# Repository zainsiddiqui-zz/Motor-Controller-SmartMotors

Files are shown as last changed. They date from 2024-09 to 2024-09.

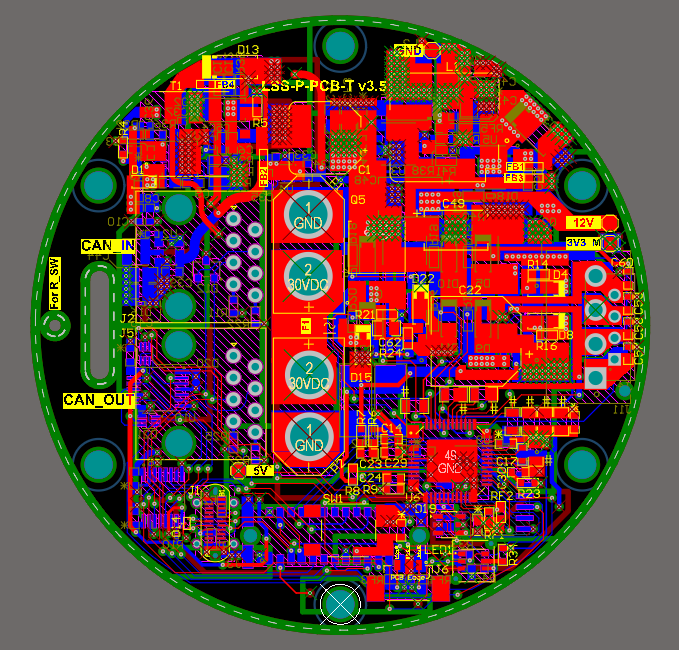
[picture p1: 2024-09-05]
Design-Files/LSS_Top_Board_v3.5/Renderings/2D_C_View.PNG

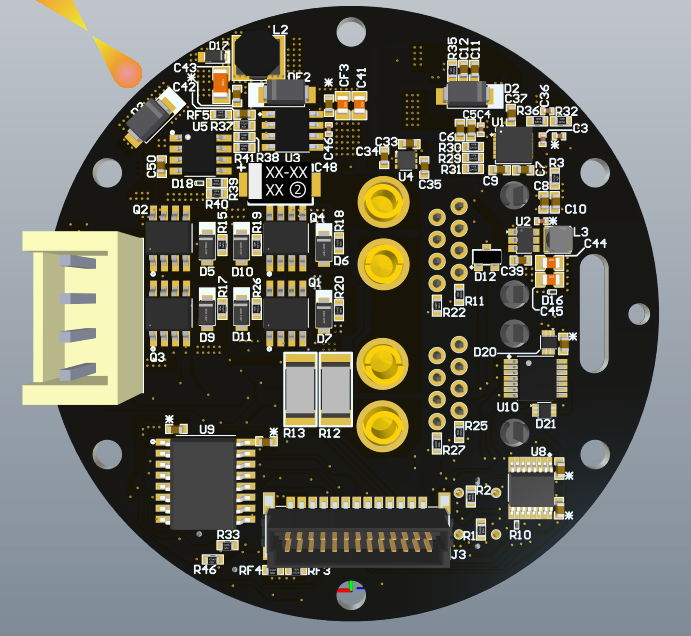
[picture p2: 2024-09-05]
Design-Files/LSS_Top_Board_v3.5/Renderings/3D_Bottom_View.PNG

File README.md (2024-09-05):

# ColeBenson-SmartMotors
 To create a smart motor system involving CAN Interface using STM32 MCU

## Firmware Upload document
https://docs.google.com/document/d/19JVTQ4CaA7uRBn9ySZQGZ3367nQTQ1OMFeYGk8ieIa8/edit#heading=h.wwlx76fb44li

## Branch Information
### main Branch
This branch contains the design submitted to client and is fabricated for testing. Firmware team should use this design for referencing with the board.

### Evaluation Branch
This branch contains the changes currently in progress. After the design is produced and fabricated, this branch will also contain corrections applied that are observed during testing of the hardware.

### Hardware-Prototype-v.3.2 Branch
This branch is referenced from Evaluation-TLE5012B branch. It will contain the final revisions / corrections needed in the hardware.

### Evaluation-TLE5012B Branch
This branch contains the changes currently in progress. After the design is produced and fabricated, this branch will also contain corrections applied that are observed during testing of the hardware. This is an extended branch of Evaluation that has TLE5012B as the magnetic encoder instead of AEAT-8800 chip.

### Hardware-Prototype-v.1 Branch
This branch contains design files for the last set of prototypes that failed to work due to noise issues.

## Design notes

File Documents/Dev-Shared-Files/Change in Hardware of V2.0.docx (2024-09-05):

# TABLE OF CONTENTS

# TABLE OF FIGURES

# HARDWARE DESIGN CHANGES

## ERROR IN 12V REGULATOR OUTPUT VOLTAGE

### PROBLEM

The first issue observed in the design was with the output of DC DC Regulator U3 which was observed to be around 30V when powered up whereas it was expected to be 12V as per calculations. After investigation, it was discovered that the FB pin was appearing as shorted to GND thus causing same voltage as the input to appear at the output. The root cause of this was discovered to be a fabrication error where resistors R38 and R41 were swapped during assembly process as can be observed in Figure

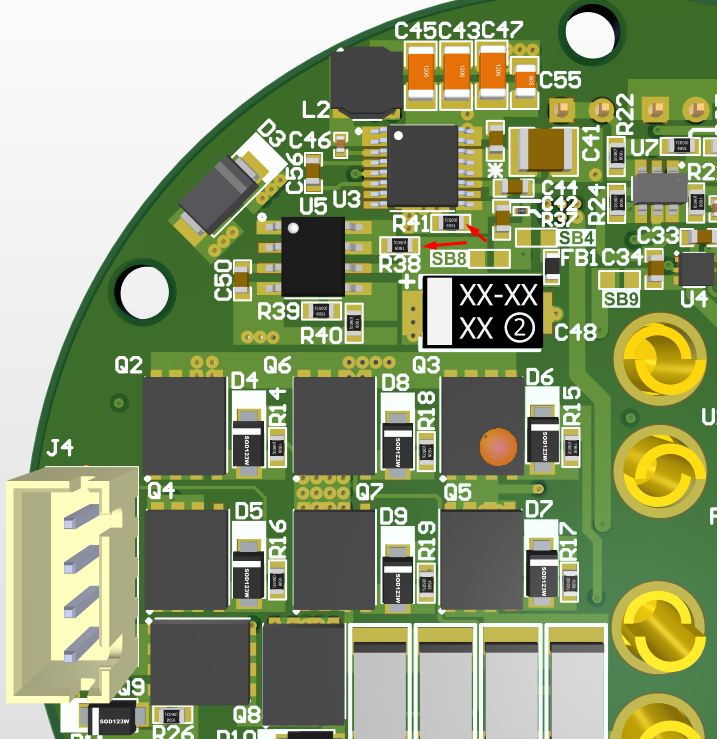
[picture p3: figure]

Figure 1 Image showing R41 and R38 swapped with each other

### SOLUTION

After swapping R38 and R41 to their actual values, the output from U3 was then observed to be correct, measured at 12.4V.

## INCORRECT OUTPUT FROM FLYBACK TRANSFORMER

### PROBLEM 01

The symbol and pin of Transformer component 750314597 was found to be incorrect causing connections to be incorrect in the schematic.

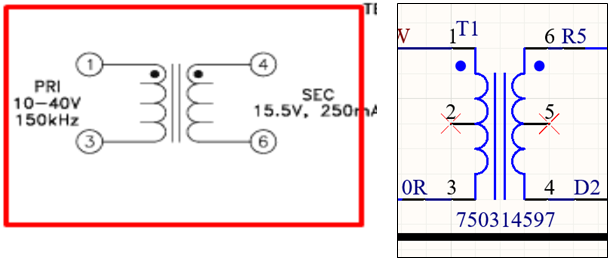
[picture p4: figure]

Figure 2 Image showing correct symbol (left) and incorrect symbol (right). Observe pin 4 and pin 6 of transformer

### SOLUTION

The other end of Resistor R5 (0 ohms) connected to ISO_GND was pulled out and connected to 3V8. Similarly, the other end of Diode D2 connected to 3V8 was pulled out and manually connected to ISO_GND.

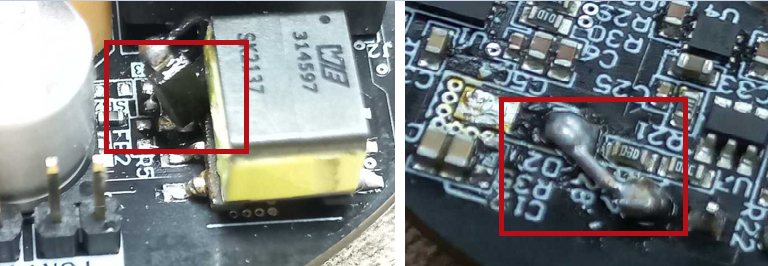
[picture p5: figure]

Figure 3 Diode placed manually on pin 6 (left) and pin 4 of transformer directly short with ISO_GND (right)

### PROBLEM 02

The next problem with this circuit was the feedback resistors were calculated incorrectly causing 8.66V to appear at the output instead of required 3.8V.

### SOLUTION

To obtain the required voltage at the output of the transformer, we need to include forward voltage drop of the secondary rectifier diode as mentioned in the datasheet. The voltage at the input of the transformer, if transformer with turns ratio of 1:1.5 (N1:N2) is selected, is calculated to be 3.0V according to the Equation 22 Pg. 24 of the LM5160ADNTR datasheet.

Figure 4 Formula for calculating Vout at the secondary of transformer

Following changes were made in hardware to achieve the desired output.

1. Change R31 to 100KΩ to set Fsw to 300 KHz, as we have set the output voltage to 3.0V at the primary side of the transformer. LM5160ADNTR Datasheet Pg#19 Equation 12.

Figure 5 Formula for setting switching frequency of transformer to 300 KHz

2. Change R4 to 7.8KΩ for the feedback network to achieve 3.0V at the output on the primary side of the fly-back transformer. The transformer will then step up the voltage and provide the isolated 3.8V at the output.

Figure 6 Formula for calculating output at the secondary of transformer 3.8V

## INCORRECT MAPPING OF SIGNAL AT INTERCONNECT

### PROBLEM

The previous phase of prototypes saw the connections to be accurate but only the incorrect soldered in reverse manner due to overlay issue from designer. This was fixed in this version of prototypes but the connections weren’t mapped according to the new changes in symbol hence causing mismatching between the signals as can be observed in Figure 7.

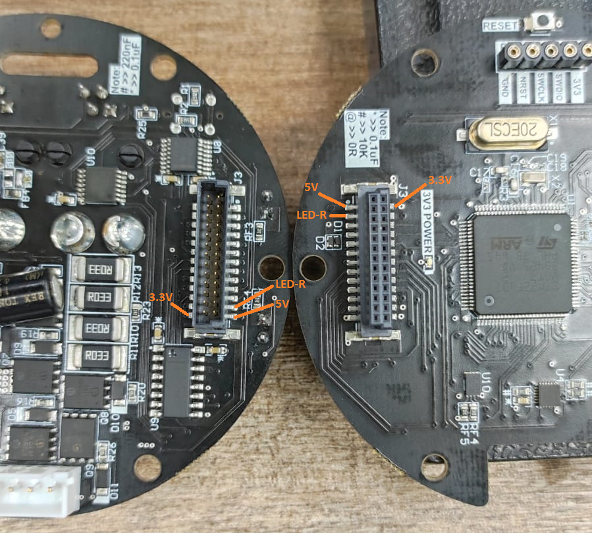
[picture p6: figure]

Figure 7 Error in mapping of interconnect signals

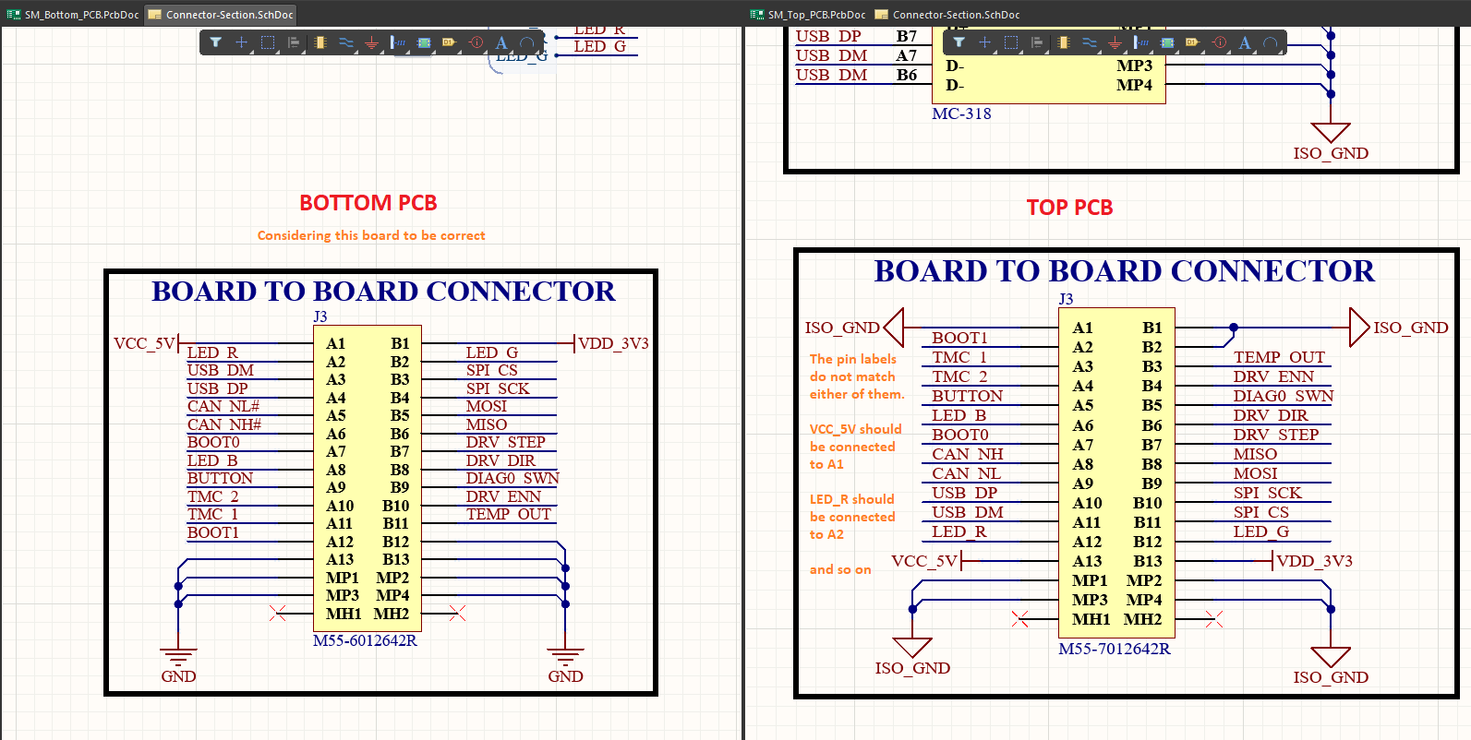
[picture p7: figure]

Figure 8 Image showing connection error with bottom PCB taken as correct reference

### SOLUTION

For the testing, the actual interconnects were removed from the board and a custom ribbon cable was manually soldered in the place to allow for further testing and proper connectivity between Top and Bottom Board

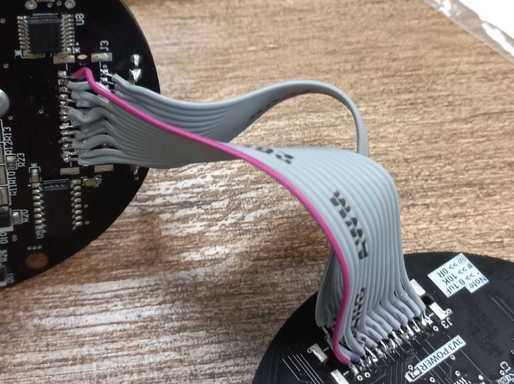
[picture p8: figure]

Figure 9 Image shows manual ribbon cable connections between Top and Bottom Board

## LED RESISTANCE MISSING

### PROBLEM

In the RGB LED LTST-G683GEBW on Top board, the current limiting resistor on the RED LED is missing.

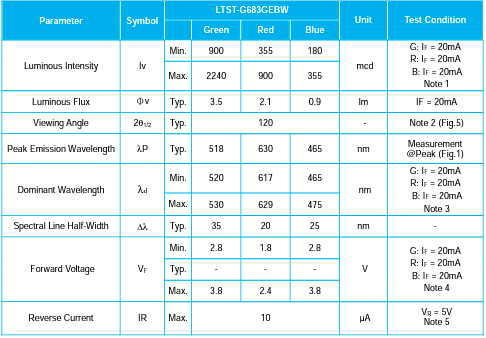
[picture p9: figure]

Figure 10 Image showing values for calculating LED series resistance

### SOLUTION

Add a resistor of 560Ω to it. Only the RED LED is troublesome. The other LEDs are working fine and properly.

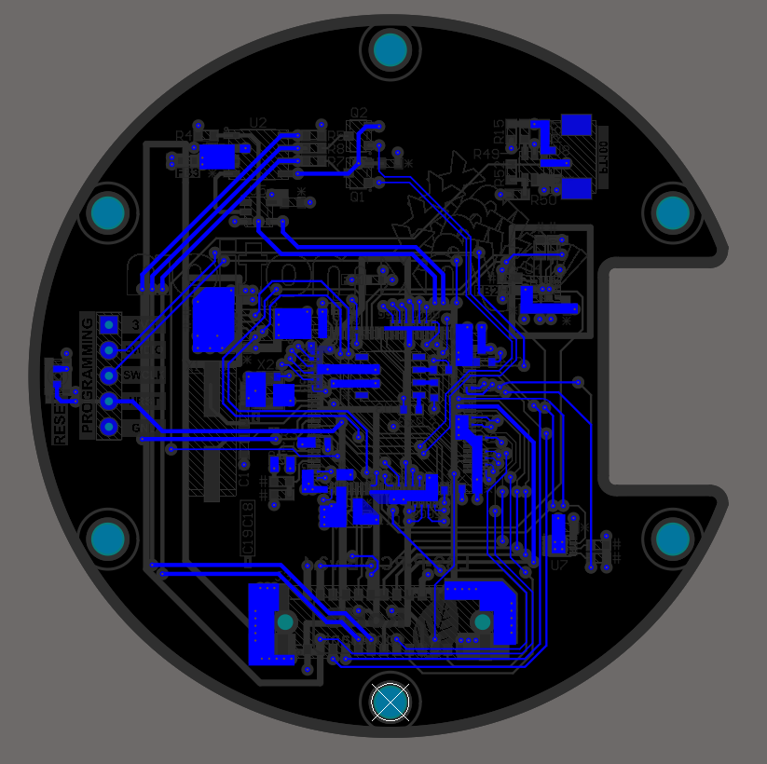
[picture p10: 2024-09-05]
Design-Files/LSS_Bottom_Board_v3.4/Renderings/2D_Bottom_View.PNG

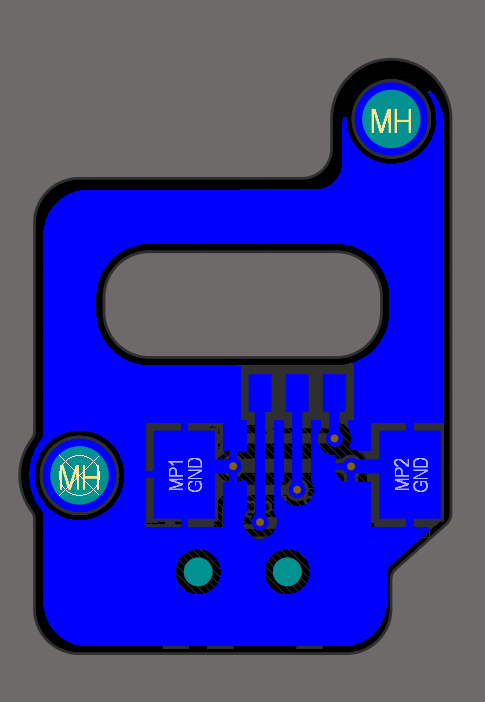
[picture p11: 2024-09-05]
Design-Files/LSS_Sub_Board_v1.1/Renderings/2D_Bottom_View.PNG.png

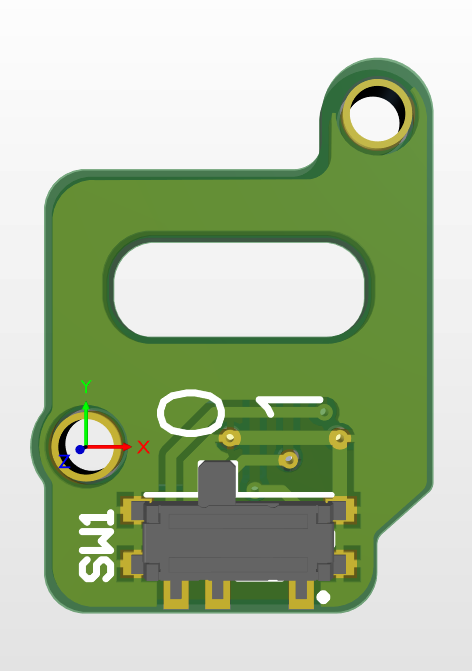
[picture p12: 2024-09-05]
Design-Files/LSS_Sub_Board_v1.1/Renderings/3D_Top_View.PNG.png

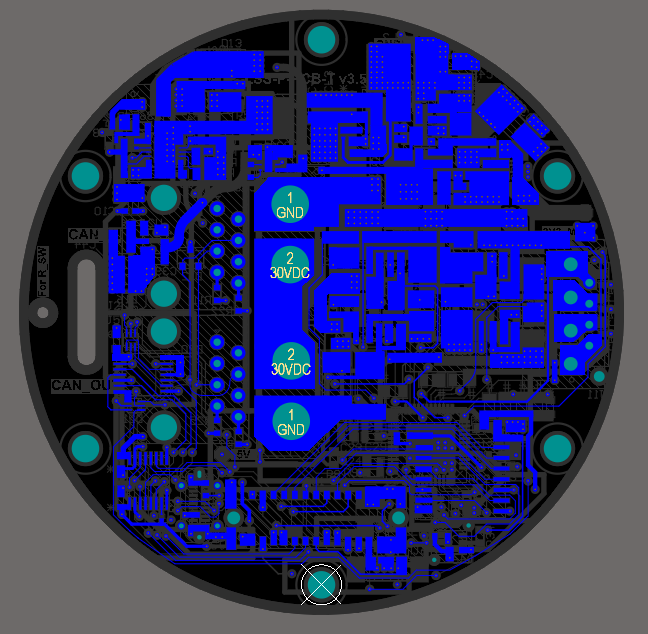
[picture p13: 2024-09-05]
Design-Files/LSS_Top_Board_v3.5/Renderings/2D_Bottom_Layer.PNG

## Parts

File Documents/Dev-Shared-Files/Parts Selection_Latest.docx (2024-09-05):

Parts Selection – Cole Ajode

1. Gyroscope
  a. ITG-3701-Operates on 3.3V (b/w 1.71 to 3.6V) – 12.74$
  b. IAM-20680HP – 16.81$
2. Encoders
  a. AEAT-6600-T16 – 7.78$
  b. AS5215OM-HMFP – 7.56$
  c. AS5134-ZSSM – 6.74$
  d. AS5047D-ATST – 6.83$
3. Motor Drivers
  a. L6207D – 6.85$
  b. DRV8860PWPR – 3.22$
  c. HIP4020IB – 3.47$
4. Voltage Regulators
  a. 24V
- DC-DC Converters
      1. DBS700B24-T – 24V/696W – 312.71000$
  b. 12V
- DC-DC Converters
      1. SIC451ED-T1-GE3 – 25A – 3.91$

Built-in 5V Regulator

      2. EHHD006A0B41Z – 72W – 6A – 30.82$
      3. TSR 1-24120SM – 12W – 1A – 9.2$
      4. UWF1212S-3WR3 – 3W – 250mA – 8.16$
      5. TES 3-2412WI – 3W – 250mA – 33.6$
      6. TIM 2-2412SM – 2W – 167mA – 28.2$
      7. TMR 1-2412SM - 1W – 83mA – 12.42$
- IC’s
      1. MPQ4436AGRE-AEC1-Z – 6A – 3.40$
      2. BDJ2FC0WFP-E2 – 1A – 0.84$
      3. MIC29151-12WU-TR – 1.5A – 4.13$
  c. 5V
    i. NCP3335ADM500R2G – 0.5A – 0.51$
    ii. MCP1826T-ADJE/DC – 1A – 0.71$
    iii. LM1085ISX-ADJ/NOPB – 3A – 2.1$
  d. 3.3V
    i. LT1584CT-3.3#PBF – 7A – 12.27$
    ii. LM1085ISX-ADJ/NOPB - 3A – 2.1$
    iii. NCP186AMX330TAG – 1A – 0.54$
    iv. NCP3335ADM330R2G – 0.5A – 0.51$
  e. 2.5V
    i. LT1584CT#PBF – 7A – 12.27$
    ii. NCP186AMX250TAG - 1A – 0.67$
    iii. NCP3337MN250R2G – 0.5A – 0.51$
  f. 1.8V
    i. NCP186AMX180TAG – 1A – 0.52$
    ii. NCP3337MN180R2G – 0.5A – 0.51$
5. Microcontroller
    i. STM32F407VGT6J – 32BIT – 1MB FLASH – 100LQFP – 10.78$

CAN Supported device

6. RJ-45 Connector
    i. 7499011121A – 6.83$ OR
    ii. E6588-WA0B44-L – 4.37$
7. USB-C Connector
    i. UJC-HP-G-SMT-TR – 1.44$
    ii. KUSBX-SMT-CS2-B30TR – 1.59$
    iii. USB4065-30-A – 3.0$
8. XT30 Connector
    i. FIT0586 – 30A/500VDC – 1.9$ (Pair of Male and Female Connectors)
    ii. XT30U-F – 0.53$ (LCSC) (https://lcsc.com/product-detail/Power-Connectors_Changzhou-Amass-Elec-XT30U-F_C99102.html)
    iii. XT30U-M – 0.47$ (LCSC) (https://lcsc.com/product-detail/Power-Connectors_Changzhou-Amass-Elec-XT30U-M_C99101.html)
    iv. XT30PW-M (https://lcsc.com/product-detail/Power-Connectors_Changzhou-Amass-Elec-XT30PW-M_C431092.html) – 0.65$ (LCSC (https://lcsc.com/product-detail/Power-Connectors_Changzhou-Amass-Elec-XT30PW-M_C431092.html))
9. DB9 Connector
    i. 2301844-2 – Female – PCB Mount – 2.40$
    ii. 182-009-213R431 – Female – PCB Mount – 2.07$

Note: All Part No.’s are from Digi-Key and prices are in USD.

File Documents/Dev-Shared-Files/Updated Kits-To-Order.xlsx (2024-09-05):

S.No | Component Name | Description | Cost | Quantity | Reference Link | Alternate Links | Remarks
1 | STM32F407VG Development Kit | DISCOVERY STM32F407/STM32F417 | $27.07 | 2 | Digikey (https://www.digikey.ca/en/products/detail/stmicroelectronics/STM32F407G-DISC1/5824404) |  | Ordered
2 | TMC5160 Development Board | BREAKOUTBOARD WITH TMC5160 | $31.00 | 2 | Digikey (https://www.digikey.ca/en/products/detail/trinamic-motion-control-gmbh/TMC5160-BOB/8440397) |  | Ordered
3 | Encoder Development Module | ANGLE 4 CLICK | $35.37 | 2 | Digikey (https://www.digikey.ca/en/products/detail/mikroelektronika/MIKROE-3130/9644672) |  | Ordered
4 | CAN Module Breakout | TI SN65HVD231 CAN TRANSCEIVER | $12.95 | 2 | ~~CopperHill~~ (https://copperhilltech.com/can-bus-mini-breakout-board/) | RobotShop (https://www.robotshop.com/en/waveshare-can-board-sn65hvd230.html) | Please check alterante Link
5 | STLink Debugger | STLINK V3 MODULAR IN-CIRCUIT DEB | $47.62 | 1 | Digikey (https://www.digikey.ca/en/products/detail/stmicroelectronics/STLINK-V3SET/9636028) |  | Ordered
6 | Jumper Wires | 40 Pins 30 cm Male To Male | $5.06 | 2 | RobotShop (https://www.robotshop.com/en/40-pins-30-cm-male-to-male-jumper-wire-flat-cable.html) |  | Order Pending
7 | Jumper Wires | 40 Pin Dual Female To Female | $2.00 | 2 | RobotShop (https://www.robotshop.com/en/40-pin-dual-female-splittable-jumper-wire-30cm.html) |  | Order Pending
8 | Jumper Wires | 40 Pin Dual Male To Female | $3.95 | 2 | RobotShop (https://www.robotshop.com/en/velleman-150mm-m-f-40-pin-jumper-wire-splittable.html) |  | Order Pending
9 | BreadBoard | Full Size - Bare Breadboard | $5.95 | 2 | RobotShop (https://www.robotshop.com/en/full-size-bare-breadboard-830-tie-point.html) |  | Order Pending
10 | Testing Hook | Patch Test Hook | $6.90 | 2 | RobotShop (https://www.robotshop.com/en/full-size-bare-breadboard-830-tie-point.html) |  | Order Pending
11 | Testing Clip | Hook Test Clip | $7.90 | 2 | RobotShop (https://www.robotshop.com/en/dfrobot-hook-test-clip-10-pk.html) |  | Order Pending
12 | PCB Holder | PCB Hand Kit | $34.95 | 2 | RobotShop (https://www.robotshop.com/en/sparkfun-third-hand-kit.html) |  | Order Pending

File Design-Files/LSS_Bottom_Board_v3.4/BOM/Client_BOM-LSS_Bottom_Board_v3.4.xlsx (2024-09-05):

# | Item Type | Designator | Description | Footprint | Manufacturer Part Number | Manufacturer | Value | Quantity | Remarks
1 | Capacitor | C1 | CAP CER 4.7UF 25V X5R 0603 | Cap0603 | CL10A475KA8NQNC | Samsung | 4.7UF | 1
2 | Capacitor | C2, C3, C4, C5, C6, C7, C8, C9, C10, C11, C15, C20, C21, C22, C33, C34, C36, C37, C50, CF1 | Cap Ceramic 0.1uF 50VDC X7R 10% SMD 0603 Paper T/R | Cap0603 | CL10B104KB8NNNC | Samsung | 0.1uF | 20 | * Symbol is used for 0.1uF in PCB
3 | Capacitor | C12 | CAP TANT 1UF 10% 16V 1206 | CAP-CASE A | TAJA105K016RNJ | Kyocera AVX | 1UF | 1
4 | Capacitor | C13, C14 | CAP, 2.2µF, 35V, 10%, X5R, 0603 | Cap 0603 | GRM188R6YA225KA12D | Murata | 2.2uF | 2
5 | Capacitor | C16, C17 | CAP 30pF NP0 0603 50 V ±5 % SMD | Cap 0603 | CC0603JRNPO9BN300 | Yageo | 30pF | 2
6 | Capacitor | C18, C19 | CAP CER 10PF 25V C0G 0201 | CAP 0201 | CGA1A2C0G1E100D030BA | TDK | 10pF | 2
7 | Diode | D12 | TVS DIODE 5V 9.8V SOD923 | SOD-923 | ESD9L5.0ST5G | ON Semiconductor | - | 1
8 | Ferrite Bead | FB1, FB2, FB3, FB4 | Ferrite Beads Multi-Layer 120Ohm 25% 100MHz 2A 45mOhm DCR 0603 Automotive T/R | Custom | MPZ1608S121ATDH5 | TDK | - | 4
9 | Connector | J1 | 1x2P 2P 1 1.25mm 2 -40℃~+85℃ Surface Mount SMD,P=1.25mm,Surface Mount，Right Angle Wire To Board / Wire To Wire Connector ROHS | Custom | 1.25-2PWB | DEALON | - | 1
10 | Connector | J3 | CONN RCPT 26POS 0.05 GOLD SMD | Custom | M55-6012642R | Harwin | - | 1
11 | Ferrite Bead | L1 | Ferrite Beads 120Ohm 25% 100MHz 1.2A 0.13Ohm DCR 0603 Automotive T/R | IND 0603 | FBMH1608HL121-TV | Taiyo Yuden | - | 1
12 | Header | P1 | MACHINE PIN SOCKET 5P 2.54MM PIT | Custom | SMC-1-05-1-GT | Adam Equipment | - | 1
13 | Transistor | Q1, Q2 | TRANS NPN 40V 0.6A SMD SOT23-3 | SOT-23 | MMBT2222A-7-F | Diodes | - | 2
14 | Resistor | R1, R6, R9, R10, R11, R12, R13, R14, R17, R18, R19, R20, R21, R22, R23, R24, R25, R26, R28, R29, R30, R31, R32, R33, R34, R35, R36, R37, R38, R39, R40, R41, R42, R43, R44, R45, R46, R47, R48 | RES SMD 0 OHM JUMPER 1/20W 0201 | Res-0201 | RC0201JR-070RL | Yageo | 0R | 39 | @ Symbol is used for 0R in PCB
15 | Resistor | R2, R27, RF1, RF2, RF3, RF4, RF5 | RES SMD 10K Ohm 1% 1/10W 0603 | Res0603 | RC0603FR-0710KL | Yageo | 10K | 7 | # Symbol is used for 10K in PCB
16 | Resistor | R3 | Res Thick Film 0201 806 Ohm 1% 1/20W ±200ppm/°C Molded SMD SMD Paper T/R | Res-0201 | RMCF0201FT806R | Stackpole Electronics | 806R | 1
17 | Resistor | R4, R5 | RES SMD 1K 0.1W 0603 75 V, Thick Film | Res0603 | RC0603JR-071KL | Yageo | 1K | 2
18 | Resistor | R7, R8 | RES SMD 57.6 OHM 1% 1/10W 0603 | Res0603 | RC0603FR-0757R6L | Yageo | 57R6 | 2
19 | Resistor | R15 | RES SMD 3.01K OHM 1% 1/10W 0603 | Res0603 | ERJ-3EKF3011V | Panasonic | 3.01K | 1
20 | Resistor | R16, R53 | RES SMD 10K Ohm 1% 1/10W 0603 | Res0603 | RC0603FR-0710KL | Yageo | DNP | 2 | Do Not Place # Symbol is used for these Resistors in PCB
21 | Resistor | R49 | RES SMD 11K, 1%, 0.1W, 0603 | Res0603 | RC0603FR-0711KL | Yageo | 11K | 1
22 | Resistor | R50 | RES SMD 12.4K OHM 1% 1/10W 0603 | Res0603 | RC0603FR-0712K4L | Yageo | 12.4K | 1
23 | Resistor | R51 | RES SMD 11.8K OHM 1% 1/10W 0603 | Res0603 | AC0603FR-0711K8L | Yageo | 11.8K | 1
24 | Resistor | R52 | RES SMD 105K OHM 1% 1/10W 0603 | Res0603 | RC0603FR-07105KL | Yageo | 105K | 1
25 | Resistor | Rx1, Rx2 | RES SMD 100 OHM 1% 1/10W 0603 | Res0603 | RC0603FR-07100RL | Yageo | 100R | 2
26 | Resistor | Rx3 | RES SMD 470 OHM 50 V, 0603 100 mW, 1%, RC Series | Res0603 | RC0603FR-07470RL | Yageo | 470R | 1
27 | Switch | SW1 | No NO J pin 50mA 3mm 100MΩ 100000 12V 250gf@±30gf 2.6mm -30℃~+85℃ 0.65mm Black Round Button Brick nogging SPST SMD Tactile Switches ROHS | Custom | GT-TC025D-H0065-L1 | G-Switch | - | 1
28 | IC | U1 | IC MCU 32BIT 512KB FLASH 100LQFP | LQFP-100 | STM32F407VET6 | STMicroelectronics | - | 1
29 | IC | U2 | IC TRANSCEIVER HALF 1/1 8SOIC | SOIC-8 | SN65HVDA1040AQDRQ1 | Texas Instruments | - | 1
30 | IC | U3 | SENSOR ANGLE 360DEG SMD | PG-DSO-8 | TLE5012BE1000 | Infineon | - | 1
31 | IC | U4 | IMUACCEL/GYROI2C/SPI14LGA | 14 LGA (2.5x3) | LSM6DSLTR | STMicroelectronics | - | 1
32 | IC | U5 | IC BUF NON-INVERT 5.5V SOT23-5 | SOT-23-5 | SN74LV1T34DBVR | Texas Instruments | - | 1
33 | IC | U6 | IC SENSOR THERMAL 3.0V 8TSSOP | 8-TSSOP | MCP9805-BE/ST | Microchip | - | 1
34 | IC | U7 | IC EEPROM 32KBIT I2C 1MHZ 8UDFN | 8-UDFN-EP (2x3) | CAT24C32HU4I-GT3 | ON Semiconductor | - | 1
35 | IC | U8 | IC OPAMP GP 1.7MHZ RRO SOT23-6 | SOT-23-6 | MAX4236EUT+T | Maxim | - | 1
36 | Crystal | X1 | CRYSTAL 20.0000MHZ 18PF SMD | Custom | HCM4920000000ABJT | CITIZEN | 20MHz | 1
37 | Crystal | X2 | Crystals 32.768KHz 7pF | Custom | ECS-.327-7-34B-C-TR | ECS International | 32.768KHz | 1
38 | Peripheral | PT100 | RTD Temp Sensor | - | - | - | -

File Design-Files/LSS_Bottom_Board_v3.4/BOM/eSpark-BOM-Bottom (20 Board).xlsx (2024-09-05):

 |  | Component list |  | Bill of Materials for Project [SM_Bottom_Board.PrjPcb]
 |  | Source Data From: |  | SM_Bottom_Board
 |  | Project: |  | SM_Bottom_Board
 |  | Variant: |  | None
# | Item Type | Designator | Description | Footprint | Manufacturer Part Number | Manufacturer | Alternate Part Number | LCSC Part Number | Value | Quantity | Quantity (20 Boards) | MOQ (20 Boards) | Links | Unit Cost (20 Boards) | Total Cost (20 Boards) | Review
1 | Capacitor | C1 | CAP CER 4.7UF 25V X5R 0603 | Cap0603 | CL10A475KA8NQNC | Samsung | - | C69335 | 4.7UF | 1 | 20 | 40 | LCSC (https://www.lcsc.com/product-detail/Multilayer-Ceramic-Capacitors-MLCC-SMD-SMT_Samsung-Electro-Mechanics-CL10A475KA8NQNC_C69335.html) | $0.0174 | $0.6960
2 | Capacitor | C2, C3, C4, C5, C6, C7, C8, C9, C10, C11, C15, C33, C34, C36, C37, C50, C22, CF1, C21 | Cap Ceramic 0.1uF 50VDC X7R 10% SMD 0603 Paper T/R | Cap0603 | CL10B104KB8NNNC | Samsung | - | C1591 | 0.1uF | 19 | 380 | 400 | LCSC (https://www.lcsc.com/product-detail/Multilayer-Ceramic-Capacitors-MLCC-SMD-SMT_Samsung-Electro-Mechanics-CL10B104KB8NNNC_C1591.html) | $0.0024 | $0.9600
3 | Capacitor | C12 | CAP TANT 1UF 10% 16V 1206 | Custom | TAJA105K016RNJ | Kyocera AVX | - | C7174 | 1uF | 1 | 20 | 25 | LCSC (https://www.lcsc.com/product-detail/span-style-background-color-ff0-Tantalum-span-Capacitors_Kyocera-AVX-TAJA105K016RNJ_C7174.html) | $0.0526 | $1.3150
4 | Capacitor | C13, C14 | CAP, 2.2µF, 35V, 10%, X5R, 0603 | Cap 0603 | GRM188R6YA225KA12D | Murata | - | C86017 | 2.2uF | 2 | 40 | 50 | LCSC (https://www.lcsc.com/product-detail/Multilayer-Ceramic-Capacitors-MLCC-SMD-SMT_Murata-Electronics-GRM188R6YA225KA12D_C86017.html) | $0.0596 | $2.9800
5 | Capacitor | C16, C17 | CAP 30pF NP0 0603 50 V ±5 % SMD | Cap 0603 | CC0603JRNPO9BN300 | Yageo | - | C113797 | 30pF | 2 | 40 | 100 | LCSC (https://www.lcsc.com/product-detail/Multilayer-Ceramic-Capacitors-MLCC-SMD-SMT_YAGEO-CC0603JRNPO9BN300_C113797.html) | $0.0026 | $0.2600
6 | Capacitor | C18, C19 | CAP CER 10PF 25V C0G 0201 | CAP 0201 | ~~CGA1A2C0G1E100D030BA~~ | TDK | UMK063CG100DTHF | C2168858 | 10pF | 2 | 40 | 50 | LCSC (https://www.lcsc.com/product-detail/Multilayer-Ceramic-Capacitors-MLCC-SMD-SMT_Taiyo-Yuden-UMK063CG100DTHF_C2168858.html) | $0.0064 | $0.3200
7 | Capacitor | C20 | CAP CER 10UF 25V X5R 0603 | Cap-0603 | C1608X5R1E106M080AC | TDK |  | C2168289 | 10uF | 1 | 20 | 21 | LCSC (https://www.lcsc.com/product-detail/Multilayer-Ceramic-Capacitors-MLCC-SMD-SMT_TDK-C1608X5R1E106M080AC_C2168289.html) | $0.4640 | $9.7440
8 | Diode | D12 | TVS DIODE 5V 9.8V SOD923 | SOD-923 | ESD9L5.0ST5G | ON Semiconductor | - | C82326 | - | 1 | 20 | 25 | LCSC (https://www.lcsc.com/product-detail/span-style-background-color-ff0-ESD-span-Protection-Devices_onsemi-ESD9L5-0ST5G_C82326.html) | $0.0617 | $1.5425
9 | Ferrite Bead | FB1, FB2, FB3, FB4 | Ferrite Beads Multi-Layer 120Ohm 25% 100MHz 2A 45mOhm DCR 0603 Automotive T/R | Ferrite0603 | MPZ1608S121ATDH5 | TDK | - | C307770 | - | 4 | 80 | 100 | LCSC (https://www.lcsc.com/product-detail/Ferrite-Beads_TDK-MPZ1608S121ATDH5_C307770.html) | $0.0280 | $2.8000
10 | Connector | J3 | CONN RCPT 26POS 0.05 GOLD SMD | Custom | M55-6012642R | Harwin | - | - | - | 1 | 20 | 22 | Mouser (https://eu.mouser.com/ProductDetail/Harwin/M55-6012642R?qs=rrS6PyfT74ceXT9Rk1eWQA%3D%3D) | $2.5100 | $55.2200
11 | Ferrite Bead | L1 | Ferrite Beads 120Ohm 25% 100MHz 1.2A 0.13Ohm DCR 0603 Automotive T/R | IND 0603 | FBMH1608HL121-TV | Taiyo Yuden | - | C515365 | - | 1 | 20 | 25 | LCSC (https://www.lcsc.com/product-detail/Ferrite-Beads_Taiyo-Yuden-FBMH1608HL121-TV_C515365.html) | $0.0876 | $2.1900
12 | LED | LED1 | LED GREEN CLEAR CHIP SMD | LED 0402 | ~~XZVG68W-2~~ | SunLED | MHT136CGCT | C401111 | - | 1 | 20 | 30 | LCSC (https://www.lcsc.com/product-detail/Light-Emitting-Diodes-span-style-background-color-ff0-LED-span_MEIHUA-MHT136CGCT_C401111.html) | $0.0379 | $1.1370
13 | Header | P1 | MACHINE PIN SOCKET 5P 2.54MM PIT | Custom | SMC-1-05-1-GT | Adam Equipment | - | - | - | 1 | 20 | 25 | Digikey (https://www.digikey.com/en/products/detail/adam-tech/SMC-1-05-1-GT/9831387) | $0.3084 | $7.7100
14 | Test Point | ~~P2, P3, P4, P5, P6, P7~~ | ~~Testing Pad 30 mil Dia~~ | ~~30 mil Test Point~~ | ~~30 mil Test Point~~ | ~~-~~ | ~~-~~ | ~~-~~ | ~~DNP~~ | ~~6~~ | ~~120~~ | ~~-~~ | ~~-~~ | ~~-~~ | ~~-~~ | ~~Do Not Mount~~
15 | Transistor | Q1, Q2 | TRANS NPN 40V 0.6A SMD SOT23-3 | SOT-23 | MMBT2222A-7-F | Diodes | - | C94515 | - | 2 | 40 | 60 | LCSC (https://www.lcsc.com/product-detail/Bipolar-Transistors-BJT_Diodes-Incorporated-MMBT2222A-7-F_C94515.html) | $0.0306 | $1.8360
16 | Resistor | R1, R9, R10, R11, R12, R13, R14, R17, R18, R19, R20, R21, R22, R23, R24, R25, R26, R28, R29, R30, R31, R32, R33, R34, R35, R36, R37, R38, R39, R40, R41, R42, R43, R44, R45, R46, R47, R48 | RES SMD 0 OHM JUMPER 1/20W 0201 | Res-0201 | RC0201JR-070RL | Yageo | - | C106228 | 0R | 38 | 760 | 800 | LCSC (https://www.lcsc.com/product-detail/Chip-Resistor-Surface-Mount_YAGEO-RC0201JR-070RL_C106228.html) | $0.0008 | $0.6400
17 | Resistor | R2, R27, RF1, RF2, RF3, RF4, RF5 | RES SMD 10K Ohm 1% 1/10W 0603 | Res0603 | RC0603FR-0710KL | Yageo | - | C98220 | 10K | 7 | 140 | 200 | LCSC (https://www.lcsc.com/product-detail/Chip-Resistor-Surface-Mount_YAGEO-RC0603FR-0710KL_C98220.html) | $0.0010 | $0.2000
18 | Resistor | R3 | Res Thick Film 0201 806 Ohm 1% 1/20W ±200ppm/°C Molded SMD SMD Paper T/R | Res-0201 | ~~RMCF0201FT806R~~ | Stackpole Electronics | 0201WMF8060TEE | C474262 | 806R | 1 | 20 | 100 | LCSC (https://www.lcsc.com/product-detail/Chip-Resistor-Surface-Mount_UNI-ROYAL-Uniroyal-Elec-0201WMF8060TEE_C474262.html) | $0.0019 | $0.1900
19 | Resistor | R4, R5 | RES SMD 1K 0.1W 0603 75 V, Thick Film | Res0603 | RC0603JR-071KL | Yageo | - | C14676 | 1K | 2 | 40 | 100 | LCSC (https://www.lcsc.com/product-detail/Chip-Resistor-Surface-Mount_YAGEO-RC0603JR-071KL_C14676.html) | $0.0010 | $0.1000
20 | Resistor | R6 | RES SMD 470 OHM 50 V, 0603 100 mW, 1%, | Res0603 | RC0603FR-07470RL | Yageo | - | C114669 | 470R | 1 | 20 | 100 | LCSC (https://www.lcsc.com/product-detail/Chip-Resistor-Surface-Mount_YAGEO-RC0603FR-07470RL_C114669.html) | $0.0013 | $0.1300
21 | Resistor | R7, R8 | RES SMD 57.6 OHM 1% 1/10W 0603 | Res0603 | ~~RC0603FR-0757R6L~~ | Yageo | CR0603-FX-57R6ELF | C203694 | 57R6 | 2 | 40 | 50 | LCSC (https://www.lcsc.com/product-detail/Chip-Resistor-Surface-Mount_BOURNS-CR0603-FX-57R6ELF_C203694.html) | $0.0027 | $0.1350
22 | Resistor | R15, R50, R51, R52 | RES SMD 4.7K OHM 1% 1/10W 0603 | Res-0603 | RC0603FR-074K7L | Yageo | - | C99782 | 4.7K | 4 | 80 | 100 | LCSC (https://www.lcsc.com/product-detail/Chip-Resistor-Surface-Mount_YAGEO-RC0603FR-074K7L_C99782.html) | $0.0012 | $0.1200
23 | Switch | SW1 | No NO J pin 50mA 3mm 100MΩ 100000 12V 250gf@±30gf 2.6mm -30℃~+85℃ 0.65mm Black Round Button Brick nogging SPST SMD Tactile Switches ROHS | Custom | GT-TC025D-H0065-L1 | G-Switch | - | C778132 | - | 1 | 20 | 30 | LCSC (https://www.lcsc.com/product-detail/Tactile-Switches_G-Switch-GT-TC025D-H0065-L1_C778132.html) | $0.0414 | $1.2420
24 | IC | U1 | IC MCU 32BIT 512KB FLASH 100LQFP | 100 LQFP | ~~STM32F407VET6~~ | STMicroelectronics | STM32F407VGT6, STM32F407VET6 | C12345, C28730 | - | 1 | 20 | 22 | LCSC (https://www.lcsc.com/product-detail/Microcontroller-Units-MCUs-MPUs-SOCs_STMicroelectronics-STM32F407VET6_C28730.html) | $10.6528 | $234.3616 | Multiple options added for MCU
25 | IC | U2 | IC TRANSCEIVER HALF 1/1 8SOIC | SOIC-8 | SN65HVDA1040AQDRQ1 | Texas Instruments | - | C188675 | - | 1 | 20 | 22 | LCSC (https://www.lcsc.com/product-detail/CAN-ICs_Texas-Instruments-SN65HVDA1040AQDRQ1_C188675.html) | $1.6387 | $36.0514
26 | IC | U3 | 18B SINGLE MAG ENC MULTIPLE AXIS | 32-QFN (5x5) | AEAT-9955 | Broadcom Limited | - | - | - | 1 | 20 | 21 | Digikey (https://www.digikey.com/en/products/detail/broadcom-limited/AEAT-9955-102/15212630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) | $21.3200 | $447.7200
27 | IC | U4 | IMUACCEL/GYROI2C/SPI14LGA | LGA-14 | ~~LSM6DSLTR~~ | STMicroelectronics | LSM6DSLTR | C126672 | - | 1 | 20 | 22 | LCSC (https://www.lcsc.com/product-detail/Attitude-Sensor-Gyroscope_STMicroelectronics-LSM6DSLTR_C126672.html) | $1.8360 | $40.3920
28 | IC | U5 | IC BUF NON-INVERT 5.5V SOT23-5 | SOT-23-5 | SN74LV1T34DBVR | Texas Instruments | - | C100024 | - | 1 | 20 | 25 | LCSC (https://www.lcsc.com/product-detail/Buffers-Drivers_Texas-Instruments-SN74LV1T34DBVR_C100024.html) | $0.2267 | $5.6675
29 | IC | U6 | IC SENSOR THERMAL 3.0V 8TSSOP | 8-TSSOP | MCP9805-BE/ST | Microchip | - | - | - | 1 | 20 | 22 | Mouser (https://eu.mouser.com/ProductDetail/Microchip-Technology/MCP9805T-BE-ST?qs=QVBMgXxBiLz7mzfqWZNLHA%3D%3D) | $1.0600 | $23.3200
30 | IC | U7 | IC EEPROM 32KBIT I2C 1MHZ 8UDFN | 8-UDFN-EP (2x3) | CAT24C32HU4I-GT3 | ON Semiconductor | - | C233772 | - | 1 | 20 | 22 | LCSC (https://www.lcsc.com/product-detail/EEPROM_onsemi-CAT24C32HU4I-GT3_C233772.html) | $0.5330 | $11.7260
31 | Crystal | X1 | CRYSTAL 20.0000MHZ 18PF SMD | Custom | HCM4920000000ABJT | CITIZEN | - | - | 20MHz | 1 | 20 | 22 | Digikey (https://www.digikey.com/en/products/detail/citizen-finedevice-co-ltd/HCM4920000000ABJT/284290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) | $0.5050 | $11.1100
32 | Crystal | X2 | Crystals 32.768KHz 7pF | Custom | ECS-.327-7-34B-C-TR | ECS International | - | - | 32.768KHz | 1 | 20 | 22 | Mouser (https://eu.mouser.com/ProductDetail/ECS/ECS-.327-7-34B-C-TR?qs=wo4x%252BUeoG8U8yBn%2Foj%2FI7w%3D%3D) | $0.6900 | $15.1800
 |  |  |  |  |  |  |  |  |  |  |  | Total Component Cost |  |  | $917.00
 |  |  |  |  |  |  |  |  |  |  |  | Single Board Cost |  |  | $45.85

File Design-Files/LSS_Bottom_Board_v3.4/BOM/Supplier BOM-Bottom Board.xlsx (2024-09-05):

 |  | Component list |  | Bill of Materials for Project [SM_Bottom_Board.PrjPcb]
 |  | Source Data From: |  | SM_Bottom_Board
 |  | Project: |  | SM_Bottom_Board
 |  | Variant: |  | None
# | Item Type | Designator | Description | Footprint | Manufacturer Part Number | Manufacturer | Value | Quantity | Links | Unit Cost (1 Boards) | Total Cost (1 Boards) | Review
1 | Capacitor | C1 | CAP CER 4.7UF 25V X5R 0603 | Cap0603 | CL10A475KA8NQNC | Samsung | 4.7UF | 1 | LCSC (https://www.lcsc.com/product-detail/Multilayer-Ceramic-Capacitors-MLCC-SMD-SMT_Samsung-Electro-Mechanics-CL10A475KA8NQNC_C69335.html) | $0.0174 | $0.0174
2 | Capacitor | C2, C3, C4, C5, C6, C7, C8, C9, C10, C11, C15, C32, C33, C34, C36, C37, C50, CF1 | Cap Ceramic 0.1uF 50VDC X7R 10% SMD 0603 Paper T/R | Cap0603 | CL10B104KB8NNNC | Samsung | 0.1uF | 18 | LCSC (https://www.lcsc.com/product-detail/Multilayer-Ceramic-Capacitors-MLCC-SMD-SMT_Samsung-Electro-Mechanics-CL10B104KB8NNNC_C1591.html) | $0.0025 | $0.0450
3 | Capacitor | C12 | CAP TANT 1UF 10% 16V 1206 | Custom | TAJA105K016RNJ | Kyocera AVX | 1uF | 1 | LCSC (https://www.lcsc.com/product-detail/span-style-background-color-ff0-Tantalum-span-Capacitors_Kyocera-AVX-TAJA105K016RNJ_C7174.html) | $0.0685 | $0.0685
4 | Capacitor | C13, C14 | CAP, 2.2µF, 35V, 10%, X5R, 0603 | Cap 0603 | GRM188R6YA225KA12D | Murata | 2.2uF | 2 | LCSC (https://www.lcsc.com/product-detail/Multilayer-Ceramic-Capacitors-MLCC-SMD-SMT_Murata-Electronics-GRM188R6YA225KA12D_C86017.html) | $0.0596 | $0.1192
5 | Capacitor | C16, C17 | CAP 30pF NP0 0603 50 V ±5 % SMD | Cap 0603 | CC0603JRNPO9BN300 | Yageo | 30pF | 2 | LCSC (https://www.lcsc.com/product-detail/Multilayer-Ceramic-Capacitors-MLCC-SMD-SMT_YAGEO-CC0603JRNPO9BN300_C113797.html) | $0.0026 | $0.0052
6 | Capacitor | C18, C19 | CAP CER 10PF 25V C0G 0201 | CAP 0201 | UMK063CG100DTHF | TDK | 10pF | 2 | LCSC (https://www.lcsc.com/product-detail/Multilayer-Ceramic-Capacitors-MLCC-SMD-SMT_Taiyo-Yuden-UMK063CG100DTHF_C2168858.html) | $0.0064 | $0.0128
7 | Diode | D1 | TVS DIODE 24VWM 41VC TO236AB | Custom | PESD2CAN,215 | Nexperia | - | 1 | LCSC (https://www.lcsc.com/product-detail/span-style-background-color-ff0-ESD-span-Protection-Devices_Nexperia-PESD2CAN-215_C75176.html) | $0.1772 | $0.1772
8 | Diode | D12 | TVS DIODE 5V 9.8V SOD923 | SOD-923 | ESD9L5.0ST5G | ON Semiconductor | - | 1 | LCSC (https://www.lcsc.com/product-detail/span-style-background-color-ff0-ESD-span-Protection-Devices_onsemi-ESD9L5-0ST5G_C82326.html) | $0.0617 | $0.0617
9 | Ferrite Bead | FB1, FB2, FB3, FB4 | Ferrite Beads Multi-Layer 120Ohm 25% 100MHz 2A 45mOhm DCR 0603 Automotive T/R | Ferrite0603 | MPZ1608S121ATDH5 | TDK | - | 4 | LCSC (https://www.lcsc.com/product-detail/Ferrite-Beads_TDK-MPZ1608S121ATDH5_C307770.html) | $0.0280 | $0.1120
10 | Connector | J3 | CONN RCPT 26POS 0.05 GOLD SMD | Custom | M55-6012642R | Harwin | - | 1 | Mouser (https://eu.mouser.com/ProductDetail/Harwin/M55-6012642R?qs=rrS6PyfT74ceXT9Rk1eWQA%3D%3D) | $2.9300 | $2.9300
11 | Ferrite Bead | L1 | Ferrite Beads 120Ohm 25% 100MHz 1.2A 0.13Ohm DCR 0603 Automotive T/R | IND 0603 | FBMH1608HL121-TV | Taiyo Yuden | - | 1 | LCSC (https://www.lcsc.com/product-detail/Ferrite-Beads_Taiyo-Yuden-FBMH1608HL121-TV_C515365.html) | $0.0876 | $0.0876
12 | LED | LED1 | LED GREEN CLEAR CHIP SMD | LED 0402 | MHT136CGCT | SunLED | - | 1 | LCSC (https://www.lcsc.com/product-detail/Light-Emitting-Diodes-span-style-background-color-ff0-LED-span_MEIHUA-MHT136CGCT_C401111.html) | $0.0399 | $0.0399
13 | Header | P1 | MACHINE PIN SOCKET 5P 2.54MM PIT | Custom | SMC-1-05-1-GT | Adam Equipment | - | 1 | Digikey (https://www.digikey.com/en/products/detail/adam-tech/SMC-1-05-1-GT/9831387) | $0.4100 | $0.4100
14 | Transistor | Q1, Q2 | TRANS NPN 40V 0.6A SMD SOT23-3 | SOT-23 | MMBT2222A-7-F | Diodes | - | 2 | LCSC (https://www.lcsc.com/product-detail/Bipolar-Transistors-BJT_Diodes-Incorporated-MMBT2222A-7-F_C94515.html) | $0.0335 | $0.0670
15 | Resistor | R1, R9, R10, R11, R12, R13, R14, R15, R16, R17, R18, R19, R20, R21, R22, R23, R24, R25, R26, R28, R29, R30, R31, R32, R33, R34, R35, R36, R37, R38, R39, R40, R41, R42, R43, R44, R45, R46, R47, R48 | RES SMD 0 OHM JUMPER 1/20W 0201 | Res-0201 | RC0201JR-070RL | Yageo | 0R | 40 | LCSC (https://www.lcsc.com/product-detail/Chip-Resistor-Surface-Mount_YAGEO-RC0201JR-070RL_C106228.html) | $0.0008 | $0.0320
16 | Resistor | R2, R27, RF1, RF2, RF3, RF4, RF5 | RES SMD 10K Ohm 1% 1/10W 0603 | Res0603 | RC0603FR-0710KL | Yageo | 10K | 7 | LCSC (https://www.lcsc.com/product-detail/Chip-Resistor-Surface-Mount_YAGEO-RC0603FR-0710KL_C98220.html) | $0.0010 | $0.0070
17 | Resistor | R3 | Res Thick Film 0201 806 Ohm 1% 1/20W ±200ppm/°C Molded SMD SMD Paper T/R | Res-0201 | 0201WMF8060TEE | Stackpole Electronics | 806R | 1 | LCSC (https://www.lcsc.com/product-detail/Chip-Resistor-Surface-Mount_UNI-ROYAL-Uniroyal-Elec-0201WMF8060TEE_C474262.html) | $0.0019 | $0.0019
18 | Resistor | R4, R5 | RES SMD 1K 0.1W 0603 75 V, Thick Film | Res0603 | RC0603JR-071KL | Yageo | 1K | 2 | LCSC (https://www.lcsc.com/product-detail/Chip-Resistor-Surface-Mount_YAGEO-RC0603JR-071KL_C14676.html) | $0.0010 | $0.0020
19 | Resistor | R6, Rx3 | RES SMD 470 OHM 50 V, 0603 100 mW, 1%,, RES SMD 470 OHM 50 V, 0603 100 mW, 1%, RC Series | Res0603 | RC0603FR-07470RL | Yageo | 470R | 2 | LCSC (https://www.lcsc.com/product-detail/Chip-Resistor-Surface-Mount_YAGEO-RC0603FR-07470RL_C114669.html) | $0.0013 | $0.0026
20 | Resistor | R7, R8 | RES SMD 57.6 OHM 1% 1/10W 0603 | Res0603 | CR0603-FX-57R6ELF | Yageo | 57R6 | 2 | LCSC (https://www.lcsc.com/product-detail/Chip-Resistor-Surface-Mount_BOURNS-CR0603-FX-57R6ELF_C203694.html) | $0.0027 | $0.0054
21 | Resistor | Rx1, Rx2 | RES SMD 100 OHM 1% 1/10W 0603 | Res0603 | RC0603FR-07100RL | Yageo | 100R | 2 | LCSC (https://www.lcsc.com/product-detail/Chip-Resistor-Surface-Mount_YAGEO-RC0603FR-07100RL_C105588.html) | $0.0009 | $0.0018
22 | ~~Solder Bridge~~ | ~~SB1, SB2, SB3, SB4, SB5, SB6, SB7, SB8~~ | ~~Solder Bridge ON~~ | ~~-~~ | ~~Solder Bridge~~ | ~~-~~ | ~~-~~ | ~~8~~ | ~~-~~ | ~~-~~ | ~~-~~
23 | Switch | SW1 | No NO J pin 50mA 3mm 100MΩ 100000 12V 250gf@±30gf 2.6mm -30℃~+85℃ 0.65mm Black Round Button Brick nogging SPST SMD Tactile Switches ROHS | Custom | GT-TC025D-H0065-L1 | G-Switch | - | 1 | LCSC (https://www.lcsc.com/product-detail/Tactile-Switches_G-Switch-GT-TC025D-H0065-L1_C778132.html) | $0.0414 | $0.0414
24 | IC | U1 | IC MCU 32BIT 512KB FLASH 100LQFP | 100 LQFP | STM32F407VET6 | STMicroelectronics | - | 1 | LCSC (https://www.lcsc.com/product-detail/Microcontroller-Units-MCUs-MPUs-SOCs_STMicroelectronics-STM32F407VET6_C28730.html) | $11.7728 | $11.7728 | Multiple options added for MCU
25 | IC | U2 | IC TRANSCEIVER HALF 1/1 8SOIC | SOIC-8 | SN65HVDA1040AQDRQ1 | Texas Instruments | - | 1 | LCSC (https://www.lcsc.com/product-detail/CAN-ICs_Texas-Instruments-SN65HVDA1040AQDRQ1_C188675.html) | $1.9012 | $1.9012
26 | IC | U3 | SENSOR ANGLE 360DEG SMD | QFN-24 | TLE5012BE1000 | Infineon | - | 1 | LCSC (https://www.lcsc.com/product-detail/Position-Sensor_Infineon-Technologies-TLE5012BE1000_C123083.html) | $3.8214 | $3.8214
27 | IC | U4 | IMUACCEL/GYROI2C/SPI14LGA | LGA-14 | LSM6DSLTR | STMicroelectronics | - | 1 | LCSC (https://www.lcsc.com/product-detail/Attitude-Sensor-Gyroscope_STMicroelectronics-LSM6DSLTR_C126672.html) | $2.0587 | $2.0587
28 | IC | U5 | IC BUF NON-INVERT 5.5V SOT23-5 | SOT-23-5 | SN74LV1T34DBVR | Texas Instruments | - | 1 | LCSC (https://www.lcsc.com/product-detail/Buffers-Drivers_Texas-Instruments-SN74LV1T34DBVR_C100024.html) | $0.2431 | $0.2431
29 | IC | U6 | IC SENSOR THERMAL 3.0V 8TSSOP | 8-TSSOP | MCP9805-BE/ST | Microchip | - | 1 | Mouser (https://eu.mouser.com/ProductDetail/Microchip-Technology/MCP9805T-BE-ST?qs=QVBMgXxBiLz7mzfqWZNLHA%3D%3D) | $1.0600 | $1.0600
30 | IC | U10 | IC EEPROM 32KBIT I2C 1MHZ 8UDFN | 8-UDFN-EP (2x3) | CAT24C32HU4I-GT3 | ON Semiconductor | - | 1 | LCSC (https://www.lcsc.com/product-detail/EEPROM_onsemi-CAT24C32HU4I-GT3_C233772.html) | $0.6428 | $0.6428
31 | Crystal | X1 | CRYSTAL 20.0000MHZ 18PF SMD | Custom | HCM4920000000ABJT | CITIZEN | 20MHz | 1 | Digikey (https://www.digikey.com/en/products/detail/citizen-finedevice-co-ltd/HCM4920000000ABJT/284290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) | $0.6100 | $0.6100
32 | Crystal | X2 | Crystals 32.768KHz 7pF | Custom | ECS-.327-7-34B-C-TR | ECS International | 32.768KHz | 1 | Mouser (https://eu.mouser.com/ProductDetail/ECS/ECS-.327-7-34B-C-TR?qs=wo4x%252BUeoG8U8yBn%2Foj%2FI7w%3D%3D) | $0.7300 | $0.7300
 |  |  |  |  |  |  |  |  | Total Component Cost |  | $27.09

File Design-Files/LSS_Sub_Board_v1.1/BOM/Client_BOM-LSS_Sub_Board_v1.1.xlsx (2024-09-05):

# | Item Type | Designator | Description | Footprint | Manufacturer Part Number | Manufacturer | Value | Quantity
1 | Right Angle JST | J1 | CONN HEADER SMD R/A 3POS 1.25MM | 532610371 | 53261-0371 | Molex | - | 1
2 | Slide Switch | SW1 | SWITCH SLIDE SPDT 300MA 6V | PCM12SMTR_ | PCM12SMTR | ITT C&K | - | 1
3 | JST Cable for J1

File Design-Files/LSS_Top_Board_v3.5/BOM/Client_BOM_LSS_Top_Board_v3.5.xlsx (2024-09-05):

# | Item Type | Designator | Description | Footprint | Manufacturer Part Number | Manufacturer | Value | Quantity | Remarks
1 | Capacitor | C1 | CAP ALUM 220UF 20% 50V SMD | EEEFT1H221AP | EEEFT1H221AP | Panasonic | 220uF | 1
2 | Capacitor | C2, C13, C15, C20, C40, C51, C52, C53, C54, C55, C61 | Cap Ceramic 0.1uF 50VDC X7R 10% SMD 0603 Paper T/R | Cap 0603 | CL10B104KB8NNNC | Samsung | 0.1uF | 11 | * Symbol is used for 0.1uF in PCB
3 | Capacitor | C3, C46 | CAP CER 10000PF 25V X7R 0402 | Cap 0402 | CC0402KRX7R8BB103 | Yageo | 10nF | 2
4 | Capacitor | C4 | CAP CER 0.47UF 50V X5R 0402 | Cap 0402 | UMK105ABJ474KV-F | Taiyo Yuden | 0.47uF | 1
5 | Capacitor | C5, C6, C14, C29, C34, C35 | CAP, 2.2µF, 35V, 10%, X5R, 0603 | Cap 0603 | GRM188R6YA225KA12D | Murata | 2.2uF | 6
6 | Capacitor | C7 | CAP CER 1UF 25V X5R 0603 | Cap 0603 | CC0603KRX5R8BB105 | Yageo | 1uF | 1
7 | Capacitor | C8, C10, C11, C12 | 10uF 35V X5R 20% Pad SMD 0603 | Cap 0603 | GRM188R6YA106MA73D | Murata | 10uF | 4
8 | Capacitor | C9 | CAP CER 0.082UF 50V X7R 0603 | Cap 0603 | CC0603KRX7R9BB823 | Yageo | 82nF | 1
9 | Capacitor | C16, C18, C19, C21, C26, C27, C28, C31 | Cap Ceramic 0.22uF 100V X7R 10% SMD 0805 125°C Embossed T/R, CAP CER 0.22UF 100V X7R 0805 | Cap0805 | 08051C224K4T2A | Kyocera AVX | 220nF | 8 | # Symbol is used for 220nF in PCB
10 | Capacitor | C17 | 0603 .022uF 100volts X7R 10% T=0.8mm | Cap 0603 | CGA3E2X7R2A223K080AA | TDK | 22nF | 1
11 | Capacitor | C22 | 220uF 63V 225mA@100KHz ±20% SMD,D10xL10.5mm Aluminum Electrolytic Capacitors - SMD ROHS | 189RV0038 | 189RV0038 | KNSCHA | 220uF | 1
12 | Capacitor | C23, C24 | CAP CER 2200PF 50V X7R 0603 | Cap-0603 | CC0603KRX7R9BB222 | Yageo | 2.2nF | 2
13 | Capacitor | C30 | CAP CER 0.47uF 50V X7R 0603 | Cap 0603 | UMK107B7474KA-TR | Taiyo Yuden | 0.47uF | 1
14 | Capacitor | C32 | CAP CER 0.1UF 50V X7R 0402 | Cap 0402 | CL05B104KB54PNC | Samsung | 0.1UF | 1
15 | Capacitor | C33 | CAP CER 4.7UF 25V X5R 0603 | Cap 0603 | CL10A475KA8NQNC | Samsung | 4.7UF | 1
16 | Capacitor | C36 | CAP CER 1000PF 100V X7R 0402 | Cap 0402 | 885012205080 | Wurth Electronics | 1000pF | 1
17 | Capacitor | C37 | CAP CER 2200PF 50V X7R 0603 | Cap 0603 | CC0603KRX7R9BB222 | Yageo | 2.2nF | 1
18 | Capacitor | C38 | CAP CER 0.1UF 100V X5R 0402 | Cap-0402 | GRM155R62A104KE14D | Murata | 0.1uf | 1
19 | Capacitor | C39 | CAP CER 10UF 25V X5R 0603 | Cap-0603 | C1608X5R1E106M080AC | TDK | 10uF | 1
20 | Capacitor | C41, C62, CF3 | CAP CER 10UF 50V X5R 0805 | Cap0805 | CL21A106KBYQNNE | Samsung | 10uF | 3
21 | Capacitor | C42 | 50V 6.8nF X7R ±10% 0603 | Cap 0603 | 0603B682K500NT | FH | 6.8nF | 1
22 | Capacitor | C43 | CAP CER 1206 47 uF 25 V ±20 % Tol. X5R | Cap1206 | GRM31CR61E476ME44L | Murata | 47uF | 1
23 | Capacitor | C44, C45 | CAP CER 22UF 35V X5R 0805 | Cap-0805 | C2012X5R1V226MT000E | TDK Corporation | 22uF | 2
24 | Capacitor | C48, C49 | CAP TANT 100UF 20% 25V 2917 | CAP- 2917 | TAJE107M025RNJ | Kyocera AVX | 100uF | 2
25 | Capacitor | C50 | CAP CER 470pF 10% X7R 50V 0603 SMD | Cap 0603 | CC0603KRX7R9BB471 | Yageo | 470pF | 1
26 | Capacitor | C57, C58, C59, C60 | CAP CER 1nF 100V X7R 0603 | Cap 0603 | CL10B102KC8NNNC | Samsung | 1nF | 4
27 | Diode | D1 | Diode Schottky 30V 1A Surface Mount USC | CUS10S30,H3F | CUS10S30,H3F | Toshiba | - | 1
28 | Diode | D2 | 500μA@100V 100V Single 600mV@1A 1A SMA Schottky Barrier Diodes (SBD) ROHS | SMA | SSL110A | Yangzhou | - | 1
29 | Diode | D3, DF2 | 40V 500mV@2A 2A SMA(DO-214AC) Schottky Barrier Diodes (SBD) ROHS | SMA | SS24A | Yangzhou | - | 2
30 | Diode | D4, D5, D6, D7, D8, D9, D10, D11 | DIODE SCHOTTKY 30V 1A SOD123F | CRS01(TE85L,Q,M) | CRS01(TE85L,Q,M) | TOSHIBA | - | 8
31 | Diode | D12 | TVS DIODE 24VWM 41VC TO236AB | SOT-23 | PESD2CAN,215 | Nexperia | - | 1
32 | Zener Diode | D13 | Single 1.5W 3.13V~3.47V 3.3V SMA Zener Diodes ROHS | SMA | 1SMA5913BT3G-MS | MSKSEMI | - | 1
33 | TVS/ESD | D14 | TVS DIODE 3.6VWM 8.4VC 3X2SON | X2-SON-3(0.6x1.3) | ESD122DMYR | Texas Instruments | - | 1
34 | Diode | D15 | TVS DEVICE HIGH VOLTAGE 1-CH 36V | SOD-123 | AZ4036-01G | Amazing | - | 1
35 | Diode | D16, D18 | DIODE BIDIR ESD X4DFN2 | 2-DFN (0.6x0.3) | ESDM2033MX4T5G | ON Semiconductor | - | 2
36 | TVS Diode | D17 | TVS DIODE 12VWM 19.9VC MICROSMP | MicroSMP | MSMP12A-M3/89A |  | - | 1
37 | ESD Diode | D19 | TVS DIODE 5.25VWM 17VC SOT23-6 | SOT-23-6 | USBLC6-4SC6 |  | - | 1
38 | ESD Diode | D20, D21 | TVS DIODE 5.25VWM 17VC SOT666 | SOT-666 | USBLC6-2P6 |  | - | 2
39 | Zener Diode | D22 | ±5% Single 15.3V~17.1V 500mW 16V SOD-123 Zener Diodes ROHS | SOD-123 | BZT52C16 | Shikues | - | 1
40 | Fuses | F1 | FUSE BOARD MOUNT 10A 50VDC 1206 | Fuse 1206 (3216 Metric) | 0685P9100-01 | Bel | - | 1
41 | Ferite Beads | FB1, FB2, FB3, FB4 | Ferrite Beads Multi-Layer 120Ohm 25% 100MHz 2A 45mOhm DCR 0603 Automotive T/R | MPZ1608S121ATDH5 | MPZ1608S121ATDH5 | TDK | - | 4
42 | Connector | J1 | USB 3.0 3A 1 Brick nogging 24 Female -35℃~+75℃ Type-C SMD USB Connectors ROHS | MC-318FB | MC-318FB | SOFNG | - | 1
43 | Ethernet Connector | J2, J5 | CONN MOD JACK 8P8C VERT UNSHLD | 855115001 | 85511-5001 | Molex | - | 2
44 | Connector | J3 | CONN HEADER SMD 26POS 1.27MM | M55-7012642R | M55-7012642R | Harwin | - | 1
45 | Connector | J4 | CONN HEADER VERT 4POS 2.5MM | B4B-XH-A(LF)(SN) | B4B-XH-A(LF)(SN) | JST | - | 1
46 | Connector | J6 | CONN HEADER SMD 3POS 1.25MM | 533980367 | 533980367 | Molex | - | 1
47 | Connector | J11 | CONN HEADER VERT 4POS 3.96MM | B4P-VH-FB-B(LF)(SN) | B4P-VH-FB-B(LF)(SN) | JST | - | 1
48 | Inductor | L1 | Inductor Power Shielded Wirewound 220uH 20% 1KHz Ferrite 1.3A 310mOhm DCR Blister T/R | SLF12575T-221M1R3-PF | SLF12575T-221M1R3-PF | TDK | 220uH | 1
49 | Inductor | L2 | 1A 33uH ±20% 356mΩ SMD,5x5x2mm Power Inductors ROHS | PNLS5020-330 | PNLS5020-330 | DMBJ | 33uH | 1
50 | Inductor | L3 | 1.5A 3.9uH ±20% 1.4A SMD,3x3mm Power Inductors ROHS | FNR3015S3R9MT | FNR3015S3R9MT | cjiang | 3.9uH | 1
51 | LED | LED1 | Standard LEDs - SMD SMD LED Red/Grn/Blue 625/1550/260 mcd | LTST-G683GEBW | LTST-G683GEBW | Vishay Lite-On | - | 1
52 | Power Connector | P1, P2 | XT60 Connector Male-Female Pair, Black (Pololu) | 2158 | 2158 | Polulo | - | 2 | Polulu (https://www.pololu.com/product/2158)
53 | ~~Test Point~~ | ~~P3, P4, P5, P6~~ | ~~Test Point ON~~ | ~~-~~ | ~~TEST POINT~~ | ~~-~~ | ~~-~~ | ~~4~~
54 | MOSFET | Q1, Q2, Q3, Q4 | 40V 6A 25mΩ@10V,6A 1.9W 1.6V@250uA 76pF@15V 2 N-Channel 1.013nF@15V 9.8nC@4.5V -55℃~+150℃@(Tj) SOP-8 MOSFETs ROHS | AO4882-MS | AO4882-MS | MSKSEMI | - | 4
55 | MOSFET | Q5 | MOSFET P-CH 60V 20A TO252 | DPAK | SQD19P06-60L_GE3 | Vishay | - | 1
56 | Resistor | R1, R2 | RES SMD 5.1K OHM 5% 1/10W 0603 | Res0603 | RC0603JR-075K1L | Yageo | 5.1K | 2
57 | Resistor | R3 | Res 0603 3.9K Ohm 1% 0.1W(1/10W) ±100ppm/°C Pad SMD T/R | Res0603 | RC0603FR-073K9L | Yageo | 3.9K | 1
58 | Resistor | R4 | 100mW 50V ±1% ±100ppm/℃ -55℃~+155℃ 7.87kΩ 0603 Chip Resistor - Surface Mount ROHS | Res0603 | RS-03K7871FT | FH | 7.87k | 1
59 | Resistor | R5, R11, R22, R25, R27, R32 | RES SMD 0R, 1%, 0.1W, 0603 | Res0603 | RC0603FR-070RL | Yageo | 0R | 6 | Addition Highlighted with RED
60 | Resistor | R6, R7, R8, R9 | RES SMD 47OHM 0.1W 0603 | Res0603 | RC0603FR-0747RL | Yageo | 47R | 4
61 | Resistor | R10 | RES SMD 4.7K OHM 1% 1/20W 0201 | Res-0201 | RC0201FR-074K7L | Yageo | 4.7K | 1
62 | Resistor | R12, R13 | 2W 50mΩ ±1% 2512 Current Sense Resistors/Shunt Resistors ROHS | RES-2512 | CRH2512FR050E04Z | Ever Ohms Tech | 50mR | 2
63 | Resistor | R14, R15, R16, R17, R18, R19, R20, R26 | 22Ω 0603 Chip Resistor - Surface Mount ROHS | Res0603 | 0603WAF220JT5E | UNI-ROYAL | 22R | 8
64 | Resistor | R21 | RES 24.9K OHM 1% 1/10W 0603 | Res0603 | RC0603FR-0724K9L | Yageo | 24.9K | 1
65 | Resistor | R23 | RES SMD 2.2OHM 0603 | Res0603 | ERJ-3GEYJ2R2V | Panasonic | 2R2 | 1
66 | Resistor | R24 | RES 20K OHM 1% 1/10W 0603 | Res0603 | RC0603FR-0720KL | Yageo | 20K | 1
67 | Resistor | R29 | RES SMD 127K OHM 1% 1/10W 0603 | Res0603 | RT0603FRE07127KL | Yageo | 127K | 1
68 | Resistor | R30, R31 | Res Thick Film 0603 100K Ohm 5% 1/10W 100ppm/C Molded SMD SMD Paper T/R | Res0603 | RC0603JR-07100KL | Yageo | 100K | 2
69 | Resistor | R33, R46 | RES SMD 51R 100mW 0603 | Res0603 | RC0603FR-0751RL | Yageo | 51R | 2
70 | Resistor | R34 | RES SMD 150OHM 1/10W 0603 | Res0603 | RC0603FR-07150RL | Yageo | 150R | 1
71 | Resistor | R35, R39 | RES SMD 2K OHM 1% 1/10W 0603 | Res0603 | RC0603FR-072KL | Yageo | 2K | 2
72 | Resistor | R36 | Res SMD 0603 51.1K Ohm 0.1% 1/10W | Res0603 | ERA-3AEB5112V | Panasonic | 51.1K | 1
73 | Resistor | R37 | 110kΩ 0603 Chip Resistor - Surface Mount ROHS | Res0603 | 0603WAD1103T5E | UNI-ROYAL | 110K | 1
74 | Resistor | R38, RF1, RF2, RF3, RF4, RF5 | RES SMD 10K Ohm 1% 1/10W 0603 | Res0603 | RC0603FR-0710KL | Yageo | 10K | 6
75 | Resistor | R40 | ±1% 1/10W Thick Film Resistors 75V ±100ppm/℃ -55℃~+155℃ 1.2kΩ 0603 Chip Resistor - Surface Mount ROHS | Res0603 | 0603WAF1201T5E | UNI-ROYAL | 1.2K | 1
76 | Resistor | R41 | ±1% 1/10W Thick Film Resistors 75V ±600ppm/℃ -55℃~+155℃ 0.33Ω 0603 Chip Resistor - Surface Mount ROHS | Res0603 | RTT03R330FTP | RALEC | 0.33R | 1
77 | Switch | SW1 | Memontary Tactile Push Button Switch 6X6X4.3 / 4.5 / 5/6/7/8/9/10 / 13mm SMD | - | Tactile Switch 13mm Actuator | WIN ELEC-TECH CO., LTD | - | 1
78 | Transformer | T1 | XFRMR ISOL BUCK DC/DC CONV SMD | 750314597 | 750314597 | Wurth Electronics Midcom | - | 1
79 | IC | U1 | IC REG BUCK FLYBCK ADJ 12WSON | LM5160ADNTR | LM5160ADNTR | Texas Instruments | - | 1
80 | IC | U2 | IC REG BUCK 3.3V 2A TSOT26 | TSOT-23-6 | AP63203WU-7 | Diodes | - | 1
81 | IC | U3 | NO Step-down type 1 Step-down 1V~29.4V 7V~42V 3A 300kHz SOIC-8_EP_150mil DC-DC Converters ROHS | 8-HTSOP-J | BD9876AEFJ-E2 | ROHM Semicon | - | 1
82 | IC | U4 | IC REG CHARGE PUMP 5V 140MA 6SON | TPS60150DRVR | TPS60150DRVR | Texas Instruments | - | 1
83 | IC | U5 | 1.5-A boost, buck, inverting switching regulator, operation from 0°C to 70°C 8-SOIC 0 to 70 | SOIC-8 | MC34063ADR | Texas Instruments | - | 1
84 | IC | U6 | IC MTR DRVR BIPOLAR 8-60V 48TQFP | 48-tqfp-ep (7x7) | TMC5160A-TA-T | Trinamic | - | 1
85 | IC | U8 | DGTL ISO 3000VRMS 4CH GP 16SSOP | 16-SSOP | ISO7740FDBQR |  | - | 1
86 | IC | U9 | AUTOMOTIVE, GENERAL-PURPOSE, 50- | 16-SOIC | ISO6762FQDWRQ1 |  | - | 1
87 | IC | U10 | IC BUS BUFFER TRI-ST QD 14TSSOP | SN74LVTH125PWR | SN74LVTH125PWR | Texas Instruments | - | 1
88 | Peripheral | LED Glass Pipe | LIGHT PIPE VERT 0.500" RND FACE | Custom | VLP-500-R | Bivar Inc. | - | 1

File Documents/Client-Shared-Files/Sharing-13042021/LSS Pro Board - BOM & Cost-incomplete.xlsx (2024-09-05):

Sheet: LSS Pro V0.2 BOM DK vs LCSC (Wo
LSS Pro Board V0.2 |  |  |  |  |  |  |  |  | 1 | 100
Part | QTY/Bd | MF SKU | Digikey SKU | Value | Manufacturer | Package | Description | Digikey | Unit Price (USD) | 100qty Price (USD) | Total Unit Price (USD) | Total 100qty Price (USD) | LCSC | Unit Price (USD) | 100qty Price (USD) | Total Unit Price (USD) | Total 100qty Price (USD) | Diff (DK-LCSC) | Chosen Source | ROHS | 100qty Price (USD) | Total 100qty Price (USD) | Packaging | Qty ordered | Order Note
Top PCB
 | 2 | A-2014-2S-4-N-R | AE10399-ND | - | Assmann WSW Components | - | CONN MOD JACK 8P8C VERT SHIELDED | https://www.digikey.ca/en/products/detail/assmann-wsw-components/A-2014-2S-4-N-R/2183650
 | 1 | 10132328-10011LF | 609-5380-1-ND | - | Amphenol ICC (FCI) | - | CONN RCPT USB3.1 TYPEC 24POS SMD | https://www.digikey.ca/en/products/detail/amphenol-icc-fci/10132328-10011LF/8555651
 | 1 | D6R90 F2 LFS | 401-1995-ND | - | C&K | - | SWITCH PUSH SPST-NO 0.1A 32V | https://www.digikey.ca/en/products/detail/c-k/D6R90-F2-LFS/1466352
Bottom PCB
U1 | 1 | STM32F413VGT6 | 497-17009-ND | - | STMicroelectronics | LQFP-100 | IC MCU 32BIT 1MB FLASH 100LQFP | https://www.digikey.ca/product-detail/en/stmicroelectronics/STM32F413VGT6/497-17009-ND/6564701 | 11.15 | 8.34 | 11.15 | 834.00 | - | - | - | - | - | - | https://www.digikey.ca/product-detail/en/stmicroelectronics/STM32F413VGT6/497-17009-ND/6564701 | TRUE | 8.34 | 834.00 | Tray |  | 0 stock DK/LCSC
U2 | 1 | AEAT-8800-Q24 | 516-3787-ND | - | Broadcom Limited | QFN-24 | ROTARY ENCODER MAGNETIC 4096PPR | https://www.digikey.ca/product-detail/en/broadcom-limited/AEAT-8800-Q24/516-3787-ND/6681014 | 8.00 | 5.99 | 8.00 | 599.00 | - | - | - | - | - | - | https://www.digikey.ca/product-detail/en/broadcom-limited/AEAT-8800-Q24/516-3787-ND/6681014 | TRUE | 5.99 | 599.00 | CT
U3 | 1 | POWERSTEP01 | 497-15441-ND | - | STMicroelectronics | VFQFPN-89 | IC MTR DRV BIPLR 3.3/5V 89VFQFPN | https://www.digikey.ca/product-detail/en/stmicroelectronics/POWERSTEP01/497-15441-ND/5237153 | 10.71 | 7.65 | 10.71 | 765.00 | https://lcsc.com/product-detail/Motor-Drivers_STMicroelectronics-POWERSTEP01_C80192.html | 10.35 | 8.49 | 10.35 | 849.00 | -84.00 | https://www.digikey.ca/product-detail/en/stmicroelectronics/POWERSTEP01/497-15441-ND/5237153 | TRUE | 7.65 | 765.00 | Tray
U4 | 1 | ICM-20600 | 1428-1147-1-ND | - | TDK InvenSense | LGA-14 | LOW-POWER, HIGH-PERFORMANCE INTE | https://www.digikey.ca/product-detail/en/tdk-invensense/ICM-20600/1428-1147-1-ND/9602942 | 3.70 | 2.01 | 3.70 | 201.00 | https://lcsc.com/product-detail/Motion-Sensors-Accelerometers_TDK-InvenSense-ICM-20600_C124140.html | 1.42 | 0.93 | 1.42 | 93.00 | 108.00 | https://lcsc.com/product-detail/Motion-Sensors-Accelerometers_TDK-InvenSense-ICM-20600_C124140.html | TRUE | 0.93 | 93.00 | CT
U5, U6 | 2 | SN74LVC1G126DCKR | 296-11606-1-ND | - | Texas Instruments | SC-70-5 | IC BUF NON-INVERT 5.5V SC70-5 | https://www.digikey.ca/product-detail/en/texas-instruments/SN74LVC1G126DCKR/296-11606-1-ND/385745 | 0.29 | 0.12 | 0.58 | 25.00 | https://lcsc.com/product-detail/Logic-Buffers-Drivers-Receivers-Transceivers_Texas-Instruments-SN74LVC1G126DCKR_C88039.html | 0.07 | 0.05 | 0.14 | 10.48 | 14.52 | https://lcsc.com/product-detail/Logic-Buffers-Drivers-Receivers-Transceivers_Texas-Instruments-SN74LVC1G126DCKR_C88039.html | TRUE | 0.05 | 10.48 | CT
PS1 | 1 | TS30042-M050QFNR | TS30042-M050QFNRCT-ND | - | Semtech Corporation | VFQFN-16 | IC REG BUCK 5V 2A 16QFN | https://www.digikey.ca/product-detail/en/semtech-corporation/TS30042-M050QFNR/TS30042-M050QFNRCT-ND/6605537 | 1.51 | 1.03 | 1.51 | 102.60 | - | - | - | - | - | - | https://www.digikey.ca/product-detail/en/semtech-corporation/TS30042-M050QFNR/TS30042-M050QFNRCT-ND/6605537 | TRUE | 1.03 | 102.60 | CT
PS2, PS3 | 2 | AP7361C-33E-13 | AP7361C-33E-13DICT-ND | - | Diodes Incorporated | SOT-223 | IC REG LINEAR 3.3V 1A SOT223 | https://www.digikey.ca/product-detail/en/diodes-incorporated/AP7361C-33E-13/AP7361C-33E-13DICT-ND/5638331 | 0.58 | 0.34 | 1.16 | 68.28 | https://lcsc.com/product-detail/Linear-Voltage-Regulators_Diodes-Incorporated-AP7361C-33E-13_C500795.html | 0.64 | 0.60 | 1.29 | 120.59 | -52.31 | https://www.digikey.ca/product-detail/en/diodes-incorporated/AP7361C-33E-13/AP7361C-33E-13DICT-ND/5638331 | TRUE | 0.34 | 68.28 | CT
PS4 | 1 | REF3133AIDBZR | 296-41483-1-ND | - | Texas Instruments | SOT-23-3 | IC VREF SERIES 3.3V SOT23-3 | https://www.digikey.ca/product-detail/en/texas-instruments/REF3133AIDBZR/296-41483-1-ND/5222876 | 2.57 | 1.74 | 2.57 | 174.20 | - | - | - | - | - | - | https://www.digikey.ca/product-detail/en/texas-instruments/REF3133AIDBZR/296-41483-1-ND/5222876 | TRUE | 1.74 | 174.20 | CT
D1 | 1 | PMEG4030ER,115 | 1727-5313-1-ND | - | Nexperia USA Inc. | SOD-123W | DIODE SCHOTTKY 40V 3A SOD123W | https://www.digikey.ca/product-detail/en/nexperia-usa-inc/PMEG4030ER115/1727-5313-1-ND/2676789 | 0.45 | 0.16 | 0.45 | 15.95 | https://lcsc.com/product-detail/Schottky-Barrier-Diodes-SBD_Nexperia-PMEG4030ER-115_C389355.html | 0.09 | 0.07 | 0.09 | 6.86 | 9.09 | https://lcsc.com/product-detail/Schottky-Barrier-Diodes-SBD_Nexperia-PMEG4030ER-115_C389355.html | TRUE | 0.07 | 6.86 | CT
D2 | 1 | ESDA6V1BC6 | 497-6635-1-ND | - | STMicroelectronics | SOT-23-6 | TVS DIODE 5V SOT23-6 | https://www.digikey.ca/product-detail/en/stmicroelectronics/ESDA6V1BC6/497-6635-1-ND/1865413 | 0.37 | 0.17 | 0.37 | 17.23 | - | - | - | - | - | - | https://www.digikey.ca/product-detail/en/stmicroelectronics/ESDA6V1BC6/497-6635-1-ND/1865413 | TRUE | 0.17 | 17.23 | CT
D3 | 1 | BAR43SFILM | 497-2515-1-ND | - | STMicroelectronics | SOT-23-3 | DIODE ARRAY SCHOTTKY 30V SOT23-3 | https://www.digikey.ca/product-detail/en/stmicroelectronics/BAR43SFILM/497-2515-1-ND/603897 | 0.37 | 0.12 | 0.37 | 12.23 | - | - | - | - | - | - | https://www.digikey.ca/product-detail/en/stmicroelectronics/BAR43SFILM/497-2515-1-ND/603897 | TRUE | 0.12 | 12.23 | CT
Temp | 1 | NTCLE203E3472GB0 | BC2457-ND | 4.7k | Vishay BC Components | Bead | THERM NTC 4.7KOHM 3977K BEAD | https://www.digikey.ca/product-detail/en/vishay-bc-components/NTCLE203E3472GB0/BC2457-ND/2230785 | 1.45 | 0.77 | 1.45 | 77.02 | - | - | - | - | - | - | https://www.digikey.ca/product-detail/en/vishay-bc-components/NTCLE203E3472GB0/BC2457-ND/2230785 | TRUE | 0.77 | 77.02 | Bulk
BUSY | 1 | LTST-C191KRKT | 160-1447-1-ND | Red | Lite-On Inc. | LED0603 | LED RED CLEAR SMD | https://www.digikey.ca/product-detail/en/lite-on-inc/LTST-C191KRKT/160-1447-1-ND/386836 | 0.26 | 0.09 | 0.26 | 9.00 | https://lcsc.com/product-detail/Light-Emitting-Diodes-LED_Lite-On-LTST-C191KRKT_C125099.html | - | 0.02 | - | 1.70 | 7.30 | https://lcsc.com/product-detail/Light-Emitting-Diodes-LED_Lite-On-LTST-C191KRKT_C125099.html | TRUE | 0.02 | 1.70 | CT
FLAG | 1 | LTST-C194TBKT | 160-1837-1-ND | Blue | Lite-On Inc. | LED0603 | LED BLUE CLEAR SMD | https://www.digikey.ca/product-detail/en/lite-on-inc/LTST-C194TBKT/160-1837-1-ND/2356236 | 0.42 | 0.14 | 0.42 | 13.50 | https://lcsc.com/product-detail/Light-Emitting-Diodes-LED_blue_C99290.html | - | 0.02 | - | 2.32 | 11.18 | https://lcsc.com/product-detail/Light-Emitting-Diodes-LED_blue_C99290.html | TRUE | 0.02 | 2.32 | CT
PWR | 1 | 5988070107F | 350-2035-1-ND | Green | Dialight | LED0603 | LED GREEN CLEAR 0603 SMD | https://www.digikey.ca/product-detail/en/dialight/5988070107F/350-2035-1-ND/1291339 | 0.42 | 0.13 | 0.42 | 13.00 | https://lcsc.com/product-detail/Light-Emitting-Diodes-LED_Lite-On-LTST-C191KGKT_C125098.html | - | 0.02 | - | 1.85 | 11.15 | https://lcsc.com/product-detail/Light-Emitting-Diodes-LED_Lite-On-LTST-C191KGKT_C125098.html | TRUE | 0.02 | 1.85 | CT
LED1, LED2, LED3, LED4, LED5, LED6 | 6 | WS2812B | 1528-1104-ND | RGB | Worldsemi | LED5050 | ADDRESS LED DISCR SER RGB | https://www.digikey.ca/product-detail/en/sparkfun-electronics/COM-16346/1568-COM-16346-ND/11630211 | - | 0.50 | - | 300.00 | https://lcsc.com/product-detail/Light-Emitting-Diodes-LED_Worldsemi-WS2812B-B_C114586.html | 0.10 | 0.07 | 0.60 | 44.46 | 255.54 | https://lcsc.com/product-detail/Light-Emitting-Diodes-LED_Worldsemi-WS2812B-B_C114586.html | TRUE | 0.07 | 44.46 | CT
Q1 | 1 | BSS138 | BSS138CT-ND | - | ON Semiconductor | SOT-23-3 | MOSFET N-CH 50V 220MA SOT-23 | https://www.digikey.ca/product-detail/en/on-semiconductor/BSS138/BSS138CT-ND/244294 | 0.26 | 0.09 | 0.26 | 8.76 | https://lcsc.com/product-detail/MOSFET_MDD-Microdiode-Electronics-BSS138_C427380.html | 0.01 | 0.01 | 0.01 | 1.50 | 7.26 | https://lcsc.com/product-detail/MOSFET_MDD-Microdiode-Electronics-BSS138_C427380.html | TRUE | 0.01 | 1.50 | CT
S1 | 1 | TL3342F160QG/TR | EG2531CT-ND | - | E-Switch | - | SWITCH TACTILE SPST-NO 0.05A 12V | https://www.digikey.ca/product-detail/en/e-switch/TL3342F160QG-TR/EG2531CT-ND/379004 | 0.65 | 0.52 | 0.65 | 51.98 | https://lcsc.com/product-detail/Tactile-Switches_SOFNG-TS-1187-1816_C183614.html | - | 0.04 | - | 4.15 | 47.83 | https://lcsc.com/product-detail/Tactile-Switches_SOFNG-TS-1187-1816_C183614.html | TRUE | 0.04 | 4.15 | CT
Y1 | 1 | NX3215SA-32.768KHZ-EXS00A-MU00525 | 644-1386-1-ND | 32.768KHz | NDK America, Inc. | 2-SMD, No Lead | CRYSTAL 32.768KHZ 6PF SMD | https://www.digikey.ca/product-detail/en/ndk-america-inc/NX3215SA-32.768KHZ-EXS00A-MU00525/644-1386-1-ND/9172114 | 0.68 | 0.50 | 0.68 | 49.74 | - | - | - | - | - | - | https://www.digikey.ca/product-detail/en/ndk-america-inc/NX3215SA-32.768KHZ-EXS00A-MU00525/644-1386-1-ND/9172114 | TRUE | 0.50 | 49.74 | CT
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

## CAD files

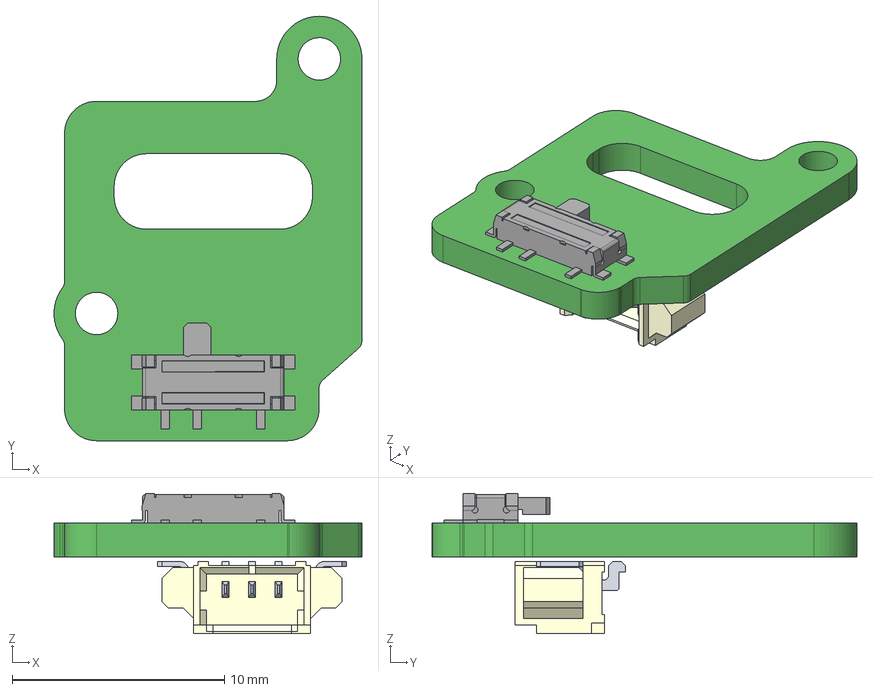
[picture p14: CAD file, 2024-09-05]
Design-Files/LSS_Sub_Board_v1.1/Supporting Files/LSS-P-PCB-S v1.1.step
14.5 x 20.0 x 6.60 mm
asd

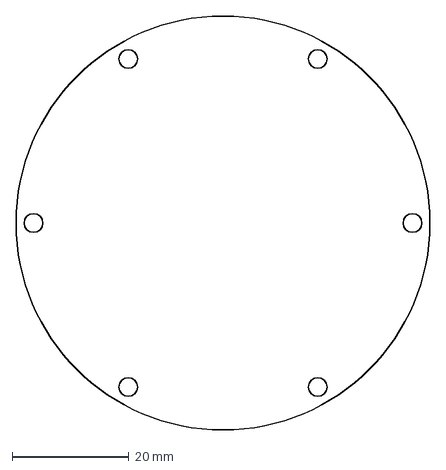
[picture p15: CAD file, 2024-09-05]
Documents/Client-Shared-Files/PCB-Dimensions.dxf
71.0 x 71.0 mm

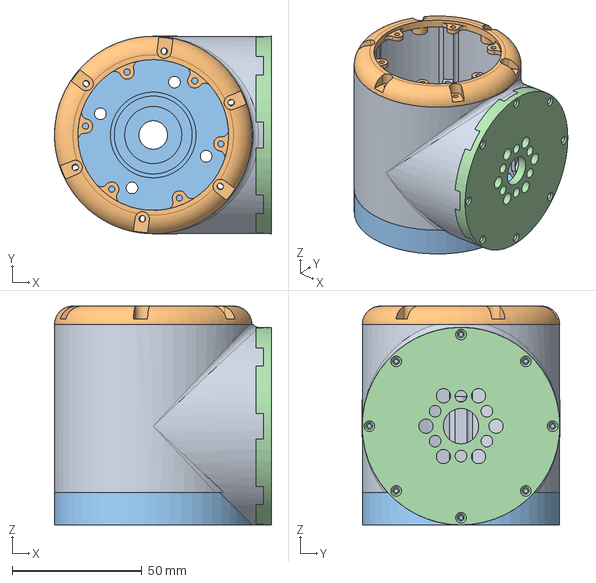
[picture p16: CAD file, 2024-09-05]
Documents/Client-Shared-Files/Sharing-04042021/Small-frame-v1.stp
83.5 x 76.0 x 84.2 mm

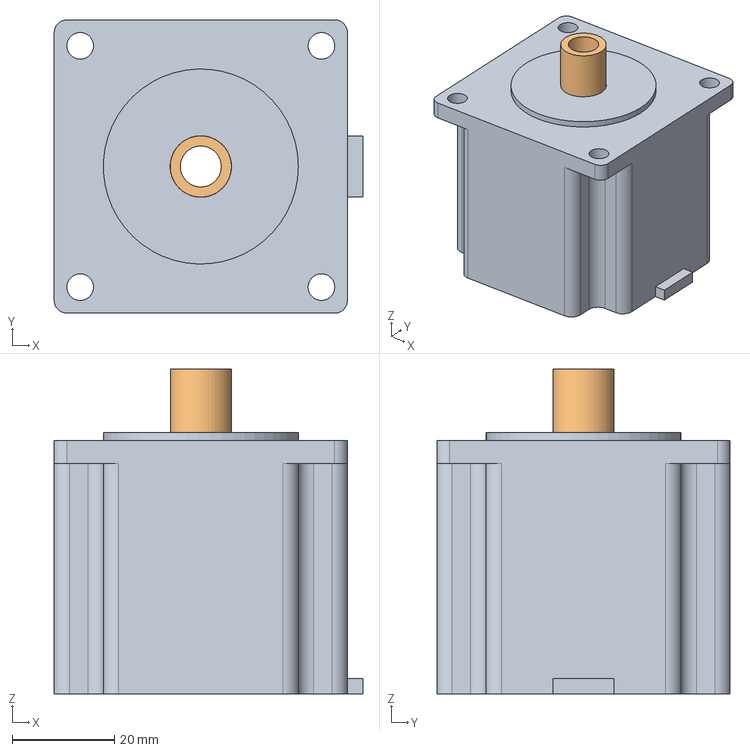
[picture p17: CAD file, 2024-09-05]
Documents/Client-Shared-Files/Sharing-13042021/JK57HS51-4204TK.stp
60.3 x 57.3 x 63.5 mm

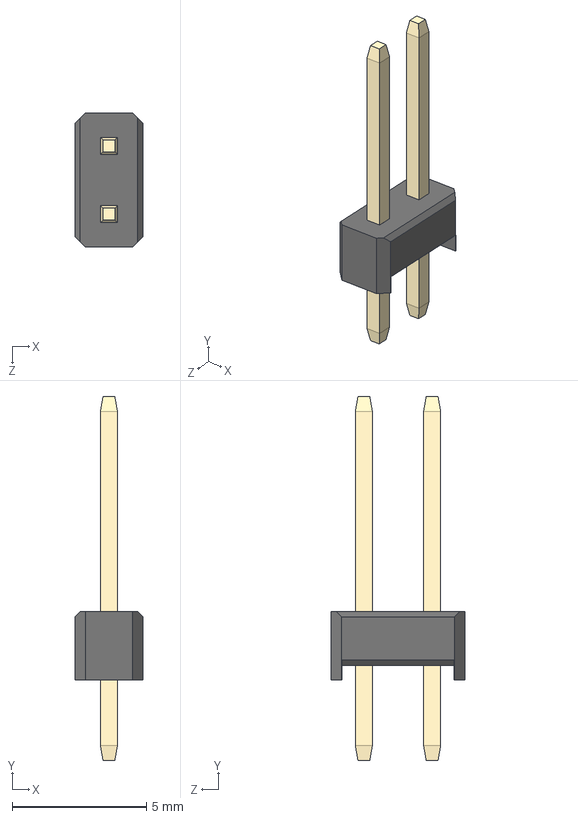
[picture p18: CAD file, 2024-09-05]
Documents/Client-Shared-Files/Sharing-13042021/LYN Pro - Electrical - 3D Parts-20210412T133957Z-001/LYN Pro - Electrical - 3D Parts/2x1 Male Pin Header.STEP
2.55 x 13.5 x 5.00 mm

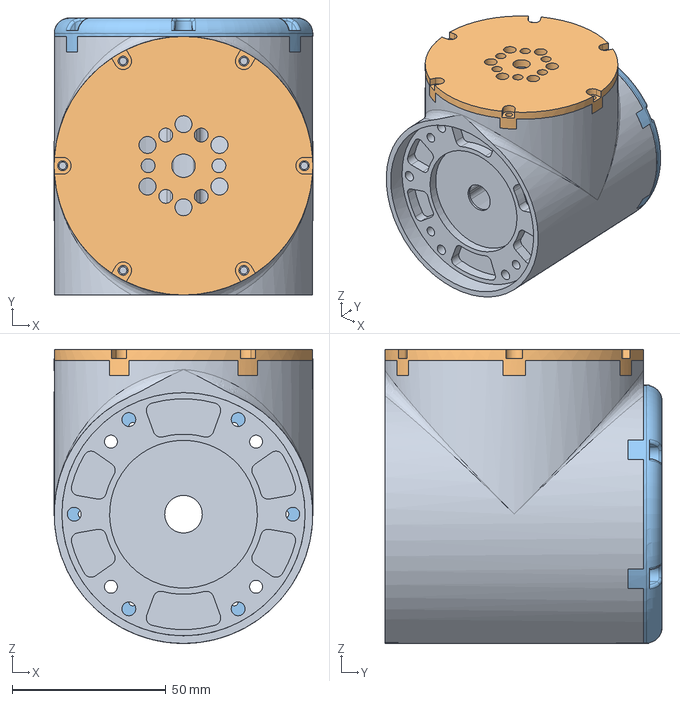
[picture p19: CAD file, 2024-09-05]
Documents/Client-Shared-Files/Sharing-04042021/Medium-frame-v1.stp
84.0 x 90.0 x 95.5 mm

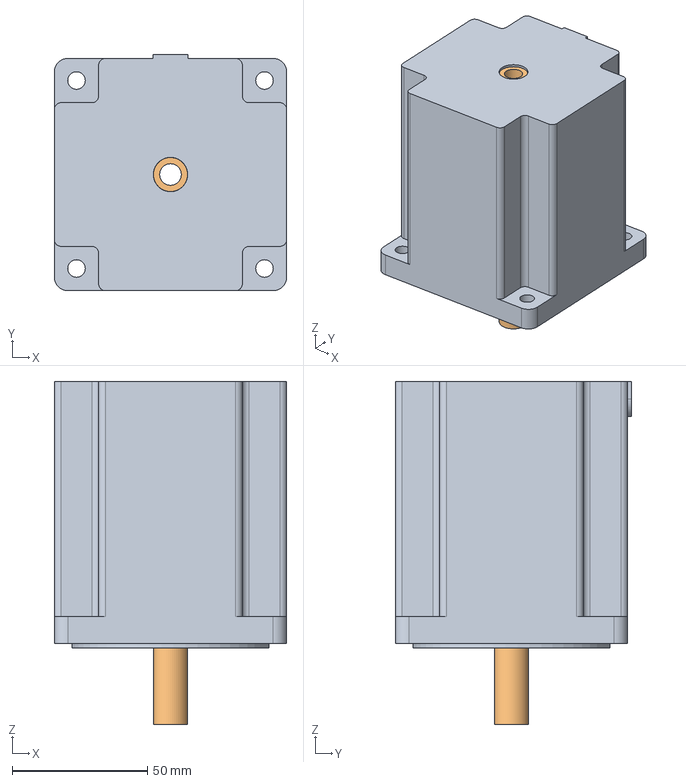
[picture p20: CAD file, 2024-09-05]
Documents/Client-Shared-Files/Sharing-13042021/JK86HS97-XXXX.stp
86.0 x 87.5 x 127.0 mm

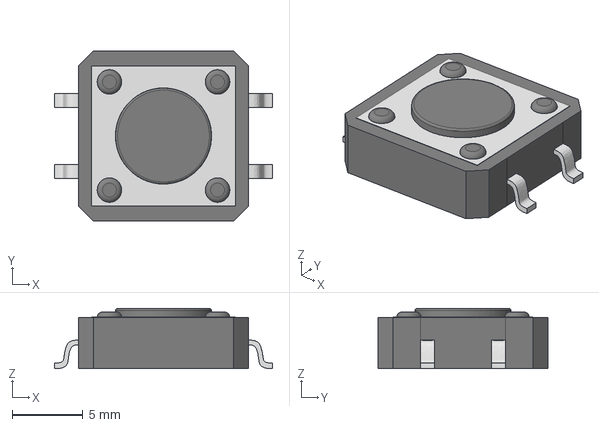
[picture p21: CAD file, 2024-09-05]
Documents/Client-Shared-Files/Sharing-13042021/LYN Pro - Electrical - 3D Parts-20210412T133957Z-001/LYN Pro - Electrical - 3D Parts/Tactal Switch - SMD (12mmx12mmx4.3mm).stp
15.4 x 12.0 x 4.25 mm

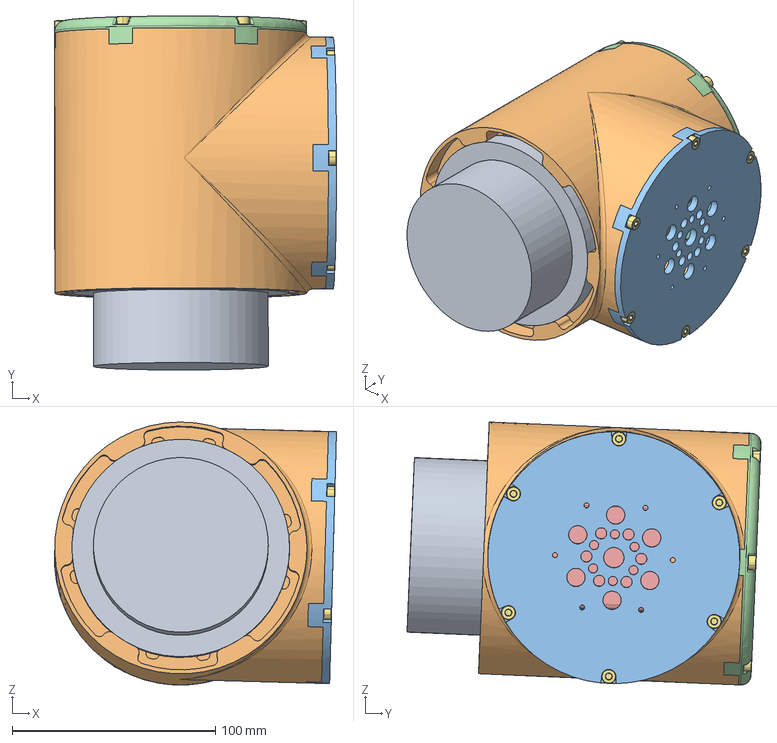
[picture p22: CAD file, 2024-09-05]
Documents/Client-Shared-Files/Sharing-04042021/large-frame-v1.stp
138.7 x 174.1 x 129.3 mm

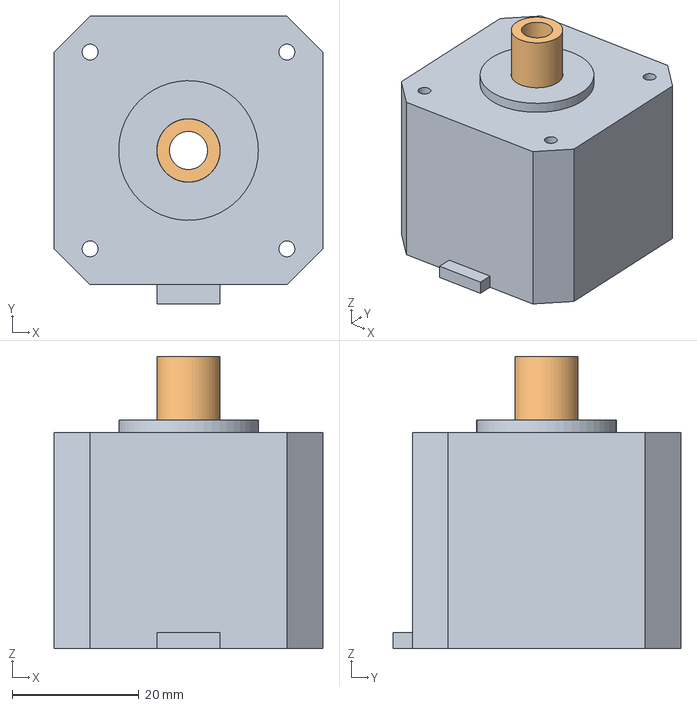
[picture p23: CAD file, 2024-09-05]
Documents/Client-Shared-Files/Sharing-13042021/JK42HS34-1334TK.stp
42.3 x 45.3 x 46.0 mm

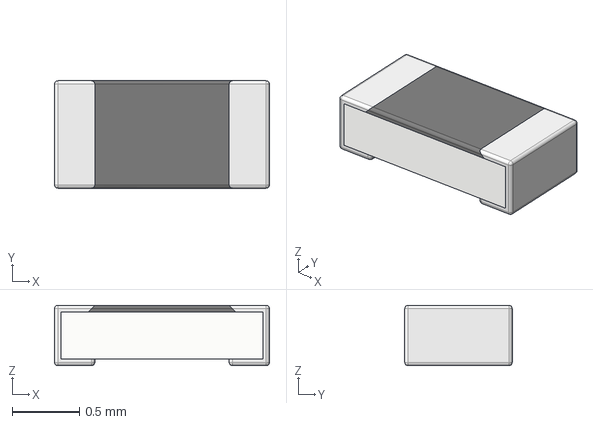
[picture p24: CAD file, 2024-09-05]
Documents/Client-Shared-Files/Sharing-13042021/LYN Pro - Electrical - 3D Parts-20210412T133957Z-001/LYN Pro - Electrical - 3D Parts/RESC0603 v2.step
1.60 x 0.8 x 0.45 mm

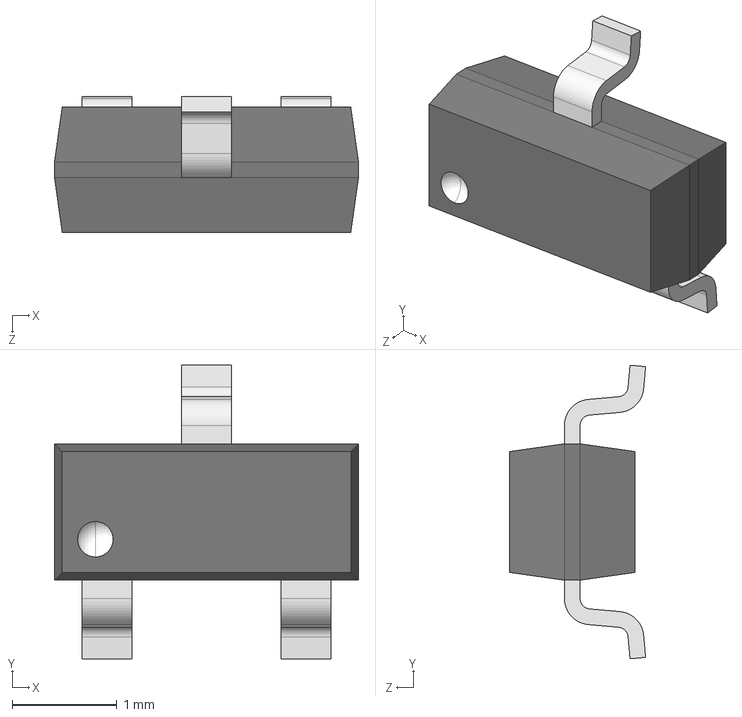
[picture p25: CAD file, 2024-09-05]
Documents/Client-Shared-Files/Sharing-13042021/LYN Pro - Electrical - 3D Parts-20210412T133957Z-001/LYN Pro - Electrical - 3D Parts/User Library-SOT23-3.step
2.90 x 2.80 x 1.30 mm

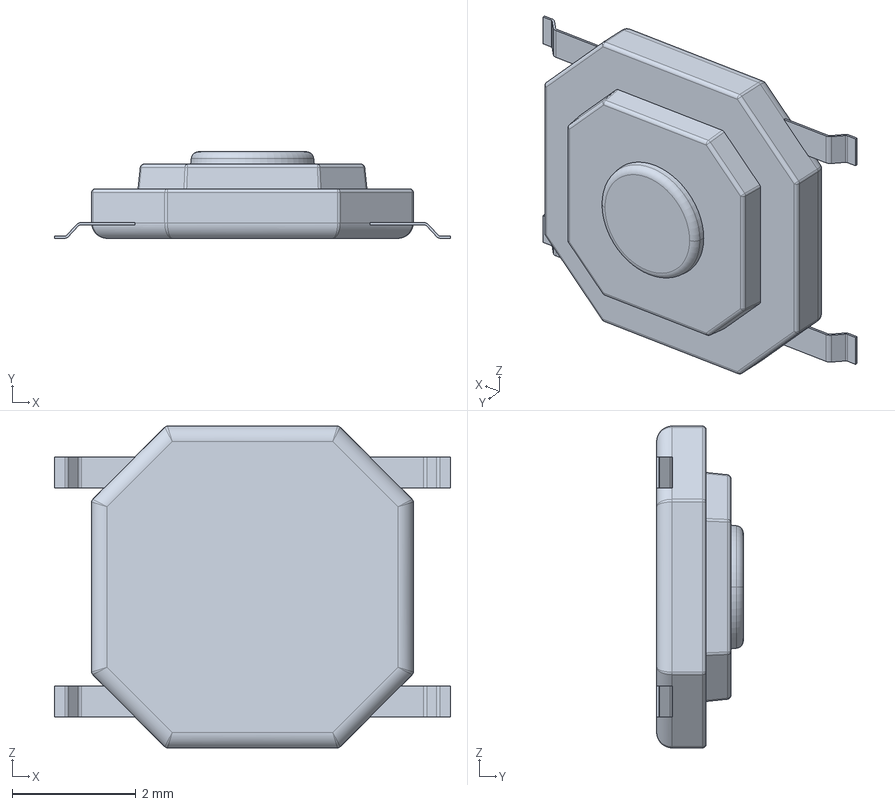
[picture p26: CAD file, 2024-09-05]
Documents/Client-Shared-Files/Sharing-13042021/LYN Pro - Electrical - 3D Parts-20210412T133957Z-001/LYN Pro - Electrical - 3D Parts/skqga.stp
6.40 x 1.40 x 5.20 mm

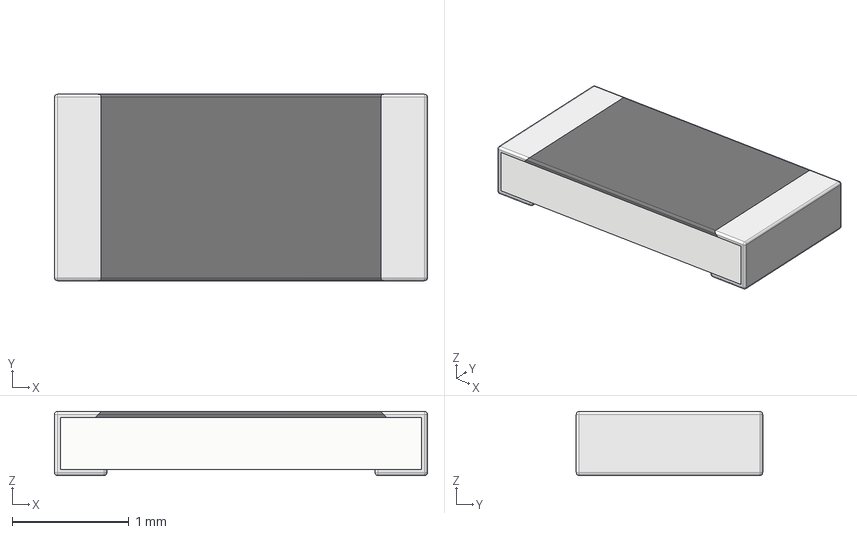
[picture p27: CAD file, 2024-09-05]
Documents/Client-Shared-Files/Sharing-13042021/LYN Pro - Electrical - 3D Parts-20210412T133957Z-001/LYN Pro - Electrical - 3D Parts/RESC1206 v1.step
3.20 x 1.60 x 0.55 mm

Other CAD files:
Design-Files/LSS_Bottom_Board_v3.4/Supporting Files/LSS-P-PCB-B v3.4.DWG
Design-Files/LSS_Top_Board_v3.5/Supporting Files/LSS-P-PCB-T v3.5.DWG
Documents/Client-Shared-Files/Sharing-13042021/LYN Pro - Electrical - 3D Parts-20210412T133957Z-001/LYN Pro - Electrical - 3D Parts/PTS525SK15.stp
Documents/Client-Shared-Files/Sharing-13042021/LYN Pro - Electrical - 3D Parts-20210412T133957Z-001/LYN Pro - Electrical - 3D Parts/Tactal Switch - SMD (12mmx12mmx6.5mm).stp
Design-Files/LSS_Sub_Board_v1.1/Supporting Files/LSS-P-PCB-S v1.1.DWG
Design-Files/LSS_Sub_Board_v1.1/Supporting Files/LSS-P-PCB-S v1.1.DXF
Design-Files/LSS_Top_Board_v3.4/Supporting Files/LSS-P-PCB-T v3.4.DWG
Documents/Client-Shared-Files/PCB-dimensions.dwg
Documents/Client-Shared-Files/Sharing-13042021/LYN Pro - Electrical - 3D Parts-20210412T133957Z-001/LYN Pro - Electrical - 3D Parts/0603_RES.stp
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

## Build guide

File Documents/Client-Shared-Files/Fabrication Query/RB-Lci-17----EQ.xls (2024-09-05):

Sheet: 问客表
Engineer Questions
客户名称: | RB-Lci-17 |  | 制作人:
客户编号: |  |  | 工厂编号: | 1701A00963A0
 |  |  | 批准:
客户传真: |  |  | 日期:
项目 | Questions | Picture | Our suggestion |  | Answer
1 | As shown in Figure 1, the four holes at the arrow. There are no pads on the top line, but have copper on the bottom line. | FIG1 | A:Make TPH for these 4 holes, and add a pad with a single side 4MIL smaller than the hole in the top layer B :pls give the reasonable suggestion. |  | We don't need PTH for these 4 holes as these holes only provide mounting support for USB connector and 20-Pin Header. So don't add pad on top layer.
2 | Please check and confirm the working file . | FIG2
3 |  | FIG3
4 |  | FIG4
5 |  | FIG5
6 |  | FIG6
7 |  | FIG7
8 |  | FIG8
9 |  | FIG9
CUSTOMER SIGNATURE: DATE:

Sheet: Fig5
TOP层线路
inner1层
inner2层
BOT层线路
BOT层阻焊

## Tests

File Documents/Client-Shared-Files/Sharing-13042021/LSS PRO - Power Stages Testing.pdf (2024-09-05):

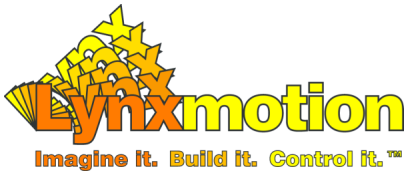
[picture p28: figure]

# LSS Pro Power Stages

Lynxmotion | LSS PRO - Power Stages
Lynxmotion | P.1

Goal

Proposed Solution (4 power stages) : Pre-prototype V1 Design
Tests
5V Switching/Buck TS30042-M050QFNR 3.3V Linear TS30042-M050
Cut-off frequency
Quality factor
Damping ratio
Pole(s)
Phase margin
Bode diagram
Pre-prototype V2 Design

# Goal

The PRO Controller PCB will have LEDs that are 5V powered and different ICs that are 3.3V powered (MCU, IMU, Enocder, Tri-state Buffers, etc..). The main power input of the PRO would be 30V-40 to power the stepper driver IC and the stepper motor. Therefore, we need to convert the main power input to a steady 5V and 3.3V which we can use for the different components mentioned above and an accurate 3.3V reference for the analog reference to obtain steady and accurate analog sensors measurements (voltage, temperature, current, etc..).

# Proposed Solution (4 power stages) :

The main 30V-40V power supply (Stage 1) will directly power the stepper driver for motor supply and the logic power of the stepper driver through its internal regulators. The main power will also convert to 5V through a 5V/2Amps switching regulator (buck converter). A buck converter (Stage 2) has been chosen for efficiency reasons as using a linear to convert 40V to 5V will have about 87.5% power loss. The 5V switching regulator output will be converted to 3.3V through two separate 3.3V linear regulators (Stage 3) : one 3.3V output will be used to power the MCU and a second 3.3V regulator to power the other 3.3V operating ICs (IMU, Encoder, buffers, CAN Transceiver, etc..). The output of the 5V switching regulator will also power the RGB Addressable LEDs. A 3.3V voltage reference chip will be used for the analog reference input of the MCU (Stage 4).
All the above is summarized in the following flow chart :

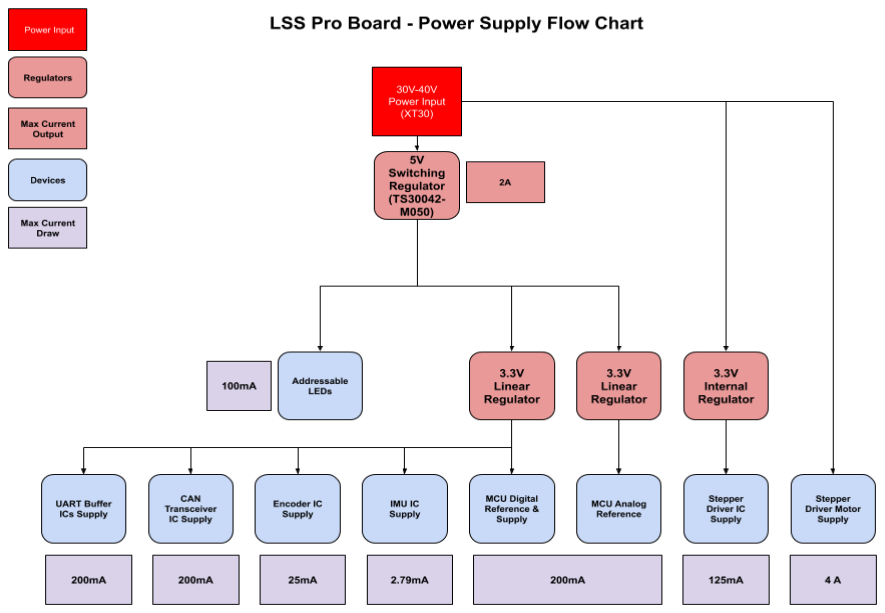
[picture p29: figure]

## Pre-prototype V1 Design

For testing purposes, we decided to design a breakout board for a 5V switching regulator in cascade with 2x 3.3V linear regulators. The 5V switching regulator chosen was the TS30042-M050QFNR which is a DC/DC synchronous fixed 5V switching regulator with 2A maximum current output, fully integrated power switches, internal compensation, and full fault protection. The switching frequency of 1MHz enables the use of smaller components resulting in minimal board space and reduced BOM costs. The 3.3V linear regulator chosen is the XC6222B331 which is a highly accurate, low noise, high ripple rejection, low dropout, and low power consumption high speed CMOS voltage regulator with 700mA maximum current output and 120mV @ Iout = 300mA dropout voltage and 65dB @ 1 KHz ripple rejection.

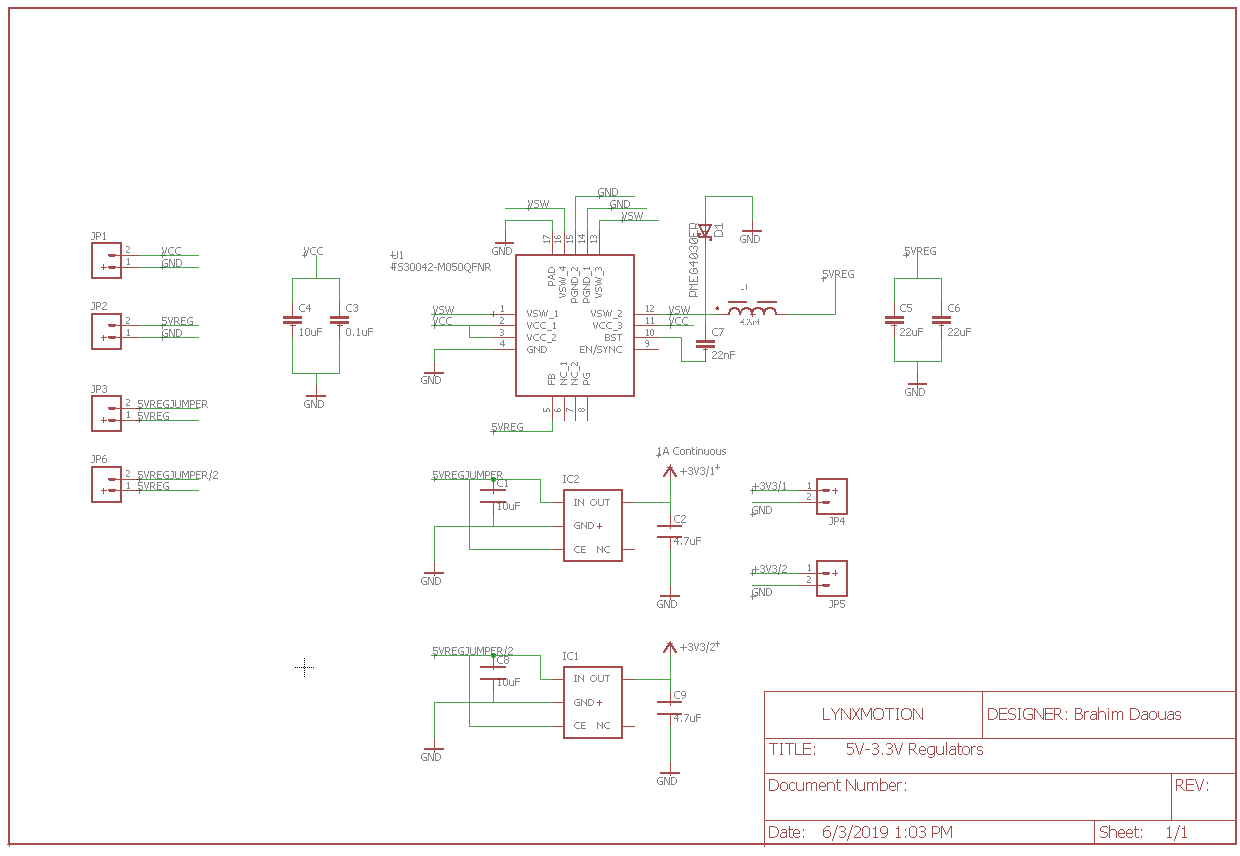
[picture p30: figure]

Schematic of the 5V/3.3V Regulators Breakout (Pre-prototype V1)

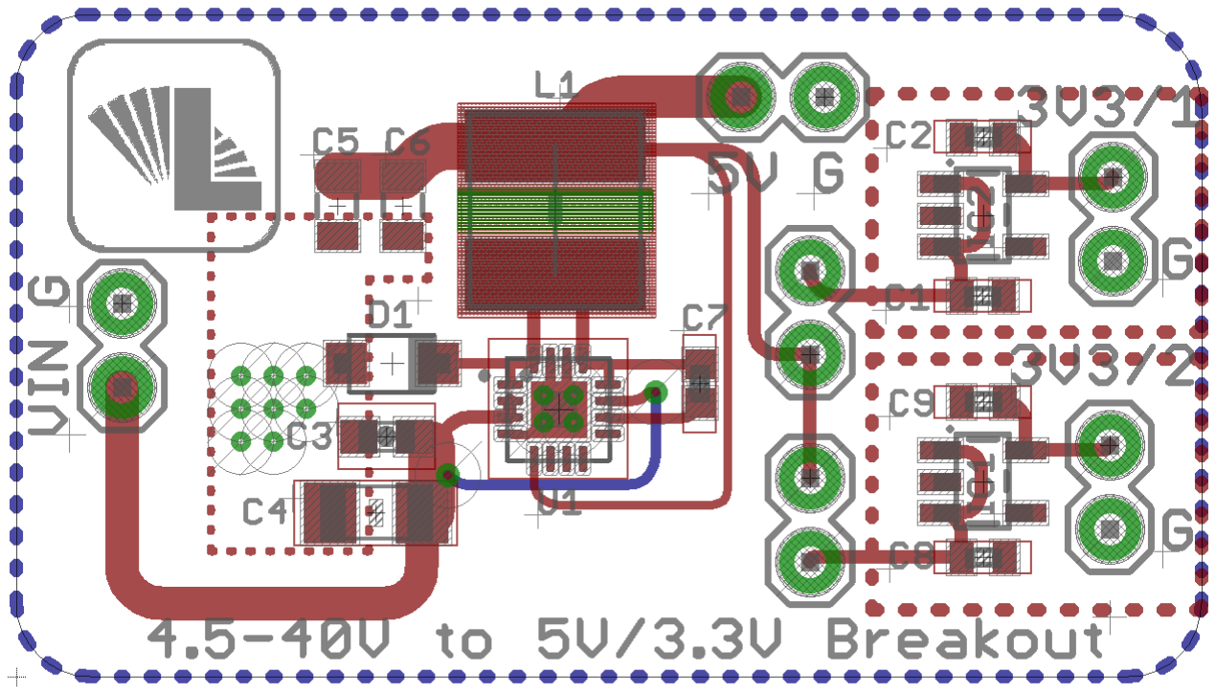
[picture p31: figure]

PCB Layout of the 5V/3.3V Regulators Breakout (Pre-prototype V1)

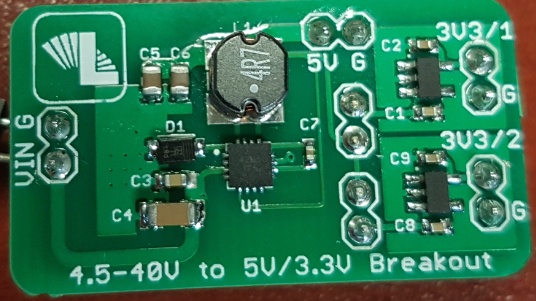
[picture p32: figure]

Assembled 5V/3.3V Regulators Breakout (Pre-prototype)

## Tests

### 5V Switching/Buck TS30042-M050QFNR

Regulator | Voltage Input (V) | Current Input (mA) | Load (mA) | Load (Ohms) V/I | Voltage Output RMS (V) | Voltage Output Max (V) | Voltage Output Min (V) | Efficiency (%) | Temperature (°C)
5V (TS30042-M050Q FNR) | 10 | 280 | 500 | ≈10 | 5.04 | 5.2 | 4.8 | 90.00% | 32
| 20 | 150 | 500 | ≈10 | 5.01 | 5.2 | 4.8 | 83.50% | 40

TS30042 5V Output (Vin = 10V, 550mA load) :

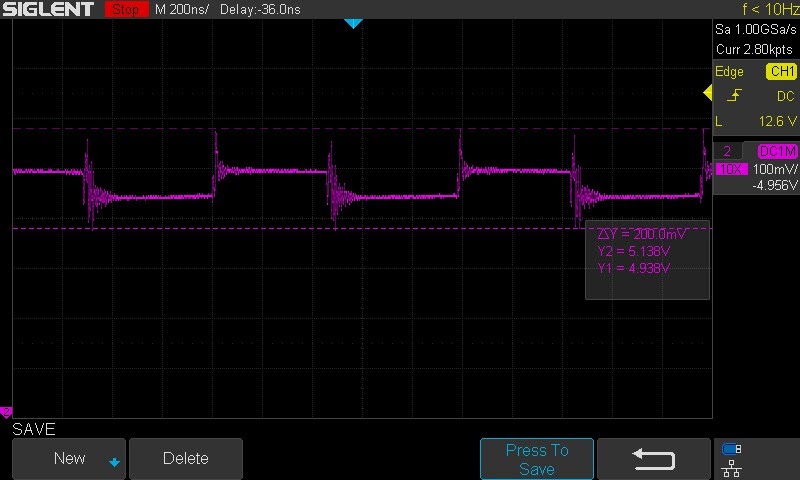
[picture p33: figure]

1MHz switching frequency with a 200mV pk-pk

2Amps max current | 30 | 100 | 500 | ≈10 | 5.02 | 5.2 | 4.8 | 83.67% | 46
| 10 | 530 | 1000 | ≈5 | 5.05 | 5.4 | 4.8 | 95.28% | 39
| 20 | 270 | 1000 | ≈5 | 5.02 | 5.4 | 4.8 | 92.96% | 49
| 30 | 190 | 1000 | ≈5 | 5.02 | 5.2 | 4.8 | 88.07% | 66
| 10 | 1100 | 1500 | ≈3.33 | 5.01 | 5.4 | 4.6 | 68.32% | 74
| 20 | 560 | 1500 | ≈3.33 | 5 | 5.2 | 4.6 | 66.96% | 95
| 30 | 390 | 1500 | ≈3.33 | 5 | 5.4 | 4.6 | 64.10% | 127

We can also notice a ringing effect on the output which is caused by the switching regulator’s output inductor that has a parasitic capacitance that forms a resonant circuit at a high frequency. With a Vin = 30V and 1000mA load, the TS30042 has a 5.02V RMS output and 88% efficiency which is acceptable for our application. The ringing effect at 1MHz with a 200mV pk-pk is also acceptable.

### 3.3V Linear TS30042-M050

XC6222B331 3.3V Output cascaded directly with the TS30042 with a 550mA load :

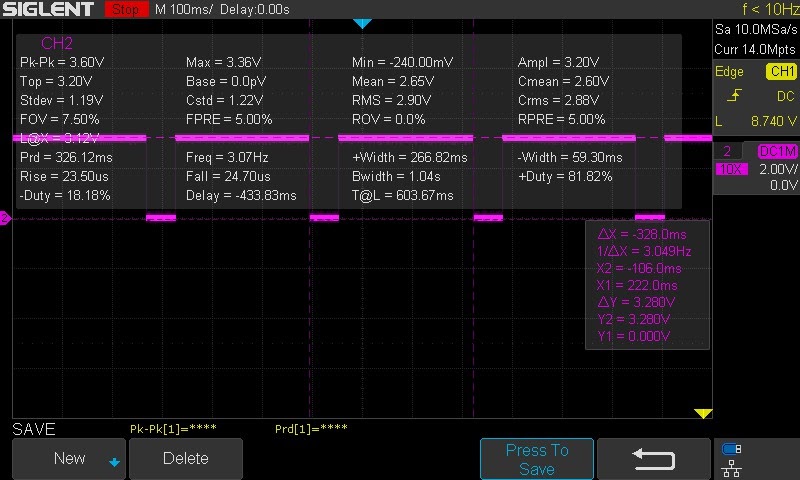
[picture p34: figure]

We noticed based on the above picture that the XC6222 is shutting down due to thermal dissipation performance.
With the TS30042 5V as input, the XC6222 temperature rise up to 102°C in about 2 seconds and starts cutting-off after 5 seconds.
We have tested the XC6222 with a fully charged Li-on battery cell (4.2V input) and we noticed that the XC6222 is not cutting-off and reaches a steady temperature of about 60°C. Therefore, we concluded that the TS30042 switching regulator 5V output has a negative effect on the XC6222 performances.

Thermal Dissipation Calculations :
The XC6222 LDO has a thermal shut down circuit inside and the circuit should be activated and cut off the voltage regulation.
VIN: 5V
VOUT: 3.3V
IOUT: 550mA
- Ploss: (5v-3.3v) x 550mA = 935mW

Page. 24 in datasheet indicates the power dissipation performance of XC6222 (SOT-23-5) + a specific PCB pattern.
The power dissipation limit at 25 deg. is 600mW.

Under their condition, mathematically the power loss is over a power dissipation performance of XC6222 (SOT-23-5)
On the other hands, SOT-89 package supports 1300mW at 25 degree C ambient temperature based upon the page 25 out of 27 on the attached data sheet.
It also makes sense that on the 2nd test with the 4.2V input, the 3.3V regulator would run cooler.

Total power dissipation = Ploss: (5v-3.3v) x 550mA = 935mW
Total power dissipation = Ploss: (4.2v-3.3v) x 550mA = 495mW

We also need to reduce the peak ripple voltage to a minimum

Therefore, 3 possible solutions will need to be verified :
- Replace the 3.3V package from SOT-25 to SOT-89

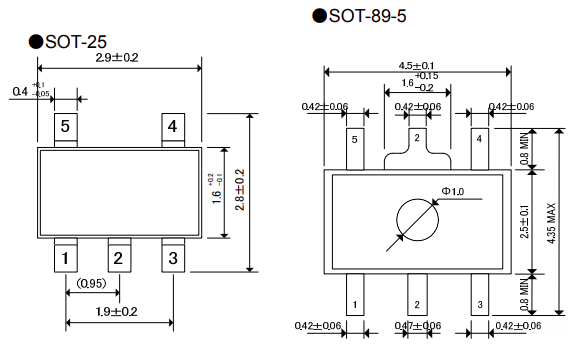
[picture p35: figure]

- Reduce the output of the 1st stage buck regulator (TI:TS30042) to 3.6Volts. The drop voltage from E2 on page 7 of the datasheet is 200mV max. This would reduce the Total power dissipation to: Ploss: (3.6v-3.3v) x 550mA = 165mW
- Reduce the 1MHz voltage ripples from the 1st stage switching regulator to a minimum with a chip bead/inductor in between the 1st stage and 2nd stage regulators

3rd Solution Tests :
Tested 2 different inductors soldered between the 1st stage and 2nd stage regulators :
- RLB0912-102KL :
https://www.digikey.ca/product-detail/en/bourns-inc/RLB0912-102KL/RLB0912-102KL-ND/2352768 (https://www.digikey.ca/product-detail/en/bourns-inc/RLB0912-102KL/RLB0912-102KL-ND/2352768)
Inductance : 1mH
Current Rating (Amps) : 400mA
Current - Saturation : 350mA
DC Resistance (DCR) : 4.3Ohm Max Q @ Freq : 55 @ 252kHz
Frequency - Self Resonant : 1.9MHz

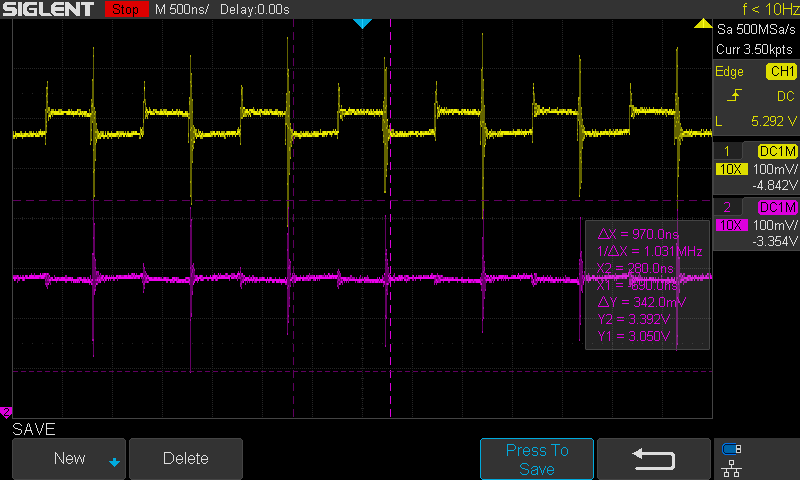
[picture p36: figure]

- RL895-102K-RC :
https://www.digikey.ca/product-detail/en/bourns-inc/RL895-102K-RC/RL895-102K-RC-ND/3193297 (https://www.digikey.ca/product-detail/en/bourns-inc/RL895-102K-RC/RL895-102K-RC-ND/3193297)
Inductance : 1mH
Current Rating (Amps) : 300mA
DC Resistance (DCR) : 1.84Ohm Max Q @ Freq : 40 @ 252kHz
Frequency - Self Resonant : 1.3MHz

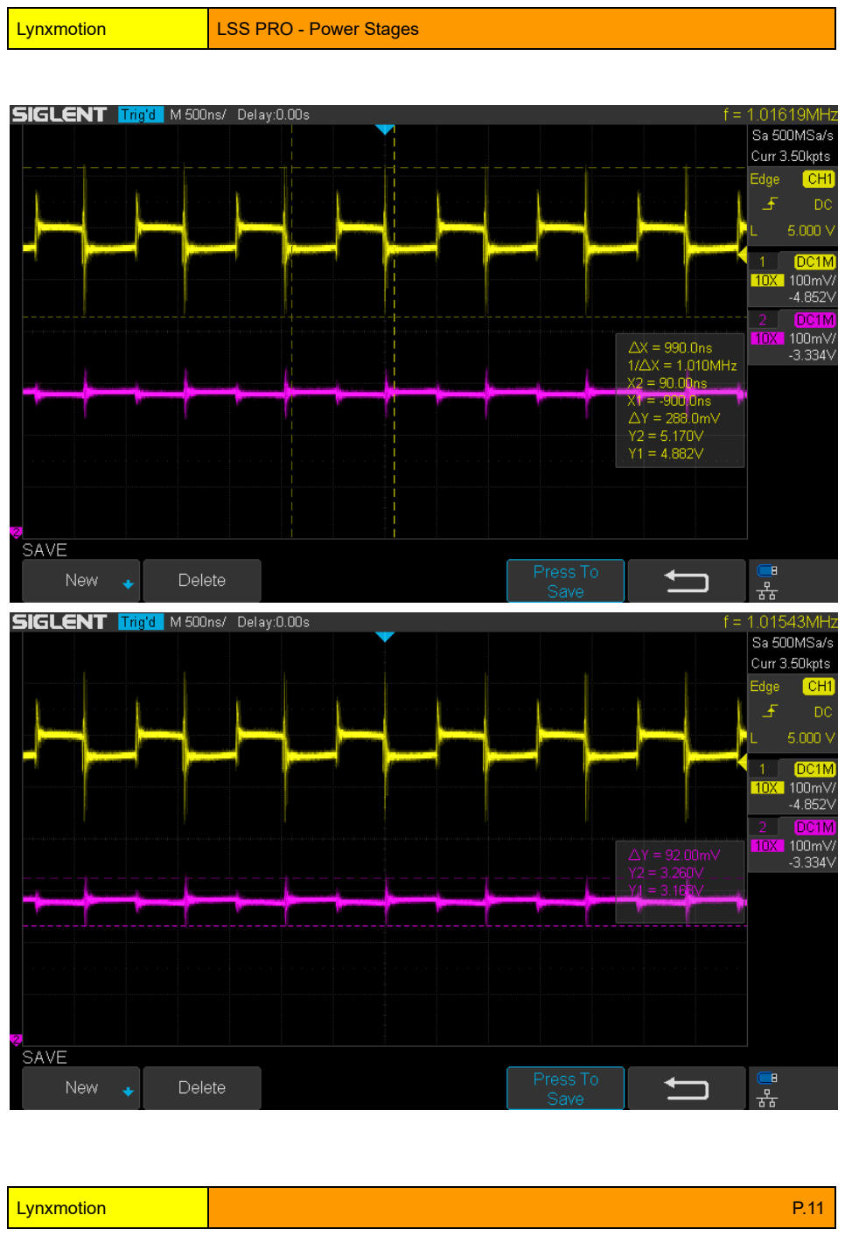
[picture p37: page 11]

3.3V output (purple) / 5V (yellow) with input & output inductors (Vin = 30V and 550mA load) :



Adding 1mH inductor in series with the 3.3V linear regulator input


3.3V linear regulator output results with the inductor


3.3V linear regulator operating temperature with the inductor

With an LC low pass filter (formed by the inductor in between the 2 regulators and the input capacitor of the 3.3V regulator), the 1MHz ripples are slightly attenuated but most importantly, the 3.3V regulator doesn’t cut-off anymore :

The LC Low pass filter created has the following characteristics :

Transfer Function:

Cut-off frequency

fc = 1591.549430919[Hz]

Quality factor

Q = 0.2

Damping ratio

ζ = 2.5

Pole(s)

p = -332.17570757239[Hz]

|p|= 332.17570757239[Hz]

p = -7625.5714470224[Hz]

|p|= 7625.5714470224[Hz]

Phase margin

pm= INF[deg] (f =0[Hz])

Bode diagram

G ( s )= | 100000000
| s ²+50000 s +100000000


Replaced the XC6222 3.3V regulator with the AMS1117 3.3V regulator which we connected to the 5V switching regulator on the pre-prototype V1 board :


The AMS1117 3.3V doesn’t cut-off on temperature and the pk-pk ripples are more attenuated. However, the AMS1117 has more voltage drop compared to the XC6222 with a 550mA load : AMS1117 3.3V output (purple) / 5V (yellow) (Vin = 10V and 550mA load) :


With these tests we have concluded that the XC6222 3.3V linear regulator is not efficient for our application. Therefore, a pre-prototype V2 will have to be designed with several others 3.3V linear regulators to be tested in cascade with the 5V switching regulator.

## Pre-prototype V2 Design

Next step was to test several 3.3V regulators in cascade with the 5V switching regulator. For this purpose, we developed a new board Pre-prototype V2 with the following 3.3V regulators :

Manufact urer Part Number | Voltage -Input (Max) | Current -Output | PSRR | Voltage Dropout (Max) | Supplier Device Package | Datasheet
TLV75733 PDBVR | 5.5V | 1A | 52dB (1kHz ~ 1MHz) | 0.475V @ 1A | SOT-23-5 | http://www.ti.com/lit/ds/symlink/tlv757p.pdf (http://www.ti.com/lit/ds/symlink/tlv757p.pdf)
AP7361C-33E-13 | 6V | 1A | 75dB ~ 55dB (1kHz ~ 10kHz) | 0.36V @ 1A | SOT-223 | https://www.diodes.com/assets/Datasheets/AP 7361C.pdf (https://www.diodes.com/assets/Datasheets/AP7361C.pdf)
AP2114H-3.3TRG1 | 6V | 1A | 65dB (100Hz ~ 1kHz) | 0.75V @ 1A | SOT-223 | https://www.diodes.com/assets/Datasheets/AP 2114.pdf (https://www.diodes.com/assets/Datasheets/AP2114.pdf)
TLV1117L V33DCYR | 5.5V | 1A | 75dB (120Hz) | 1.3V @ 800mA | SOT-223-4 | http://www.ti.com/lit/ds/symlink/tlv1117lv.pdf (http://www.ti.com/lit/ds/symlink/tlv1117lv.pdf)



PCB Layout of the 5V/3.3V Regulators Breakout (Pre-prototype V2)


Assembled 5V/3.3V Regulators Breakout (Pre-prototype V2)

3 versions of the Pre-prototype V2 have been assembled for testing with 3 different 5V output chip bead L2 :
- Pre-prototype V2/1 : 120 Ohms @ 100MHz
- Pre-prototype V2/2 : 300 Ohms @ 100MHz
- Pre-prototype V2/3 : 100 Ohms @ 100MHz

Tests have shown that the Pre-prototype V2/2 board had an overall better 3.3V output stability than the two other boards
Complete test results are shown in this sheet : https://docs.google.com/spreadsheets/d/145N4n2y6rkgCv3jdxKm-5fOuP1pSTkM7ndF6-NQ_sXc/edit#gid=1868966053 (https://docs.google.com/spreadsheets/d/145N4n2y6rkgCv3jdxKm-5fOuP1pSTkM7ndF6-NQ_sXc/edit)

Also, the AP7361C-33E-13 3.3V regulator seems to have the best 3.3V performances in terms of PSRR (power supply rejection ratio) and stability on the Pre-prototype V2/2 board compared to the other 3.3V regulators :


AP7361C-33E-13 3V3/2 Output


AP2114H-3.3TRG1 3V3/3 Output


TLV1117LV33DCYR 3V3/4 Output

Based on these results, we chose to use 1x TS30042-M050QFNR 5V regulator to power the LEDs from the input power supply of 12V-40V, 2x AP7361C-33E-13 to power the 3.3V IC (MCU, IMU, Encoder, Tri-state Buffers, etc..) and 1x REF3133AIDBZR as a 3.3V reference for the MCU’s ADC.

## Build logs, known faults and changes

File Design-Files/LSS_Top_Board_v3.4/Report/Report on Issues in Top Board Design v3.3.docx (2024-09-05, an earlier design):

POSSIBLE SUGESSTIONS IN TOP BOARD DESIGN – V3.3.

POINT NO. 1.

Area of split plane (VCC_3V3_M) is small in PCB. It is better to increase its width.

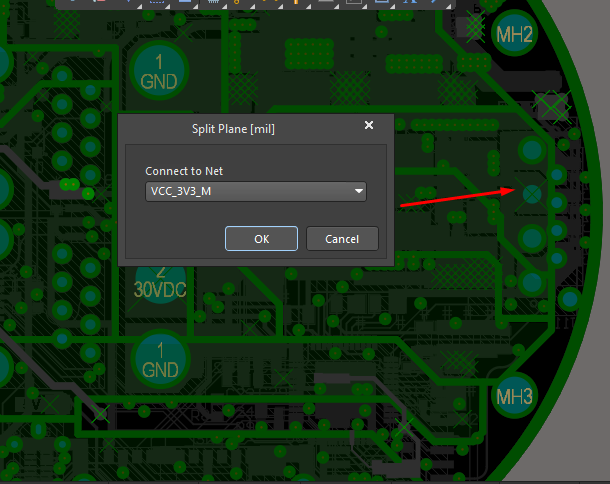
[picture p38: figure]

POINT NO. 2.

Copper Fill having VDD_3V3 net is somewhat close to main power rail (30VDC) in PCB. Having more gap between the two is recommended.

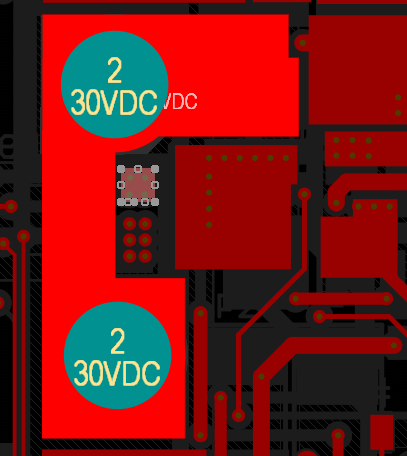
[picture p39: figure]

POINT NO. 3.

Better to add more ESD and TVS Diodes in the design. Currently only present in CAN signals. It should be implemented for Power rails and Motor Drivers signals too. As shown in image below.

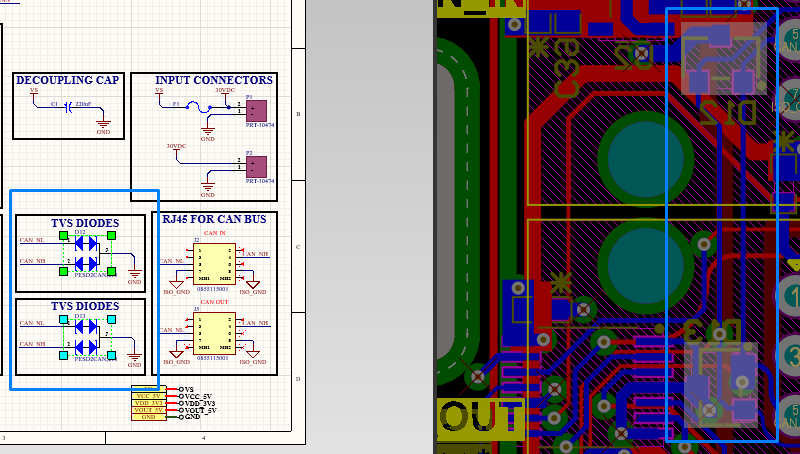
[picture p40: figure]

POINT NO. 4.

Isolators connections directions are correct but their power sides are mixed up in all isolator ICs.

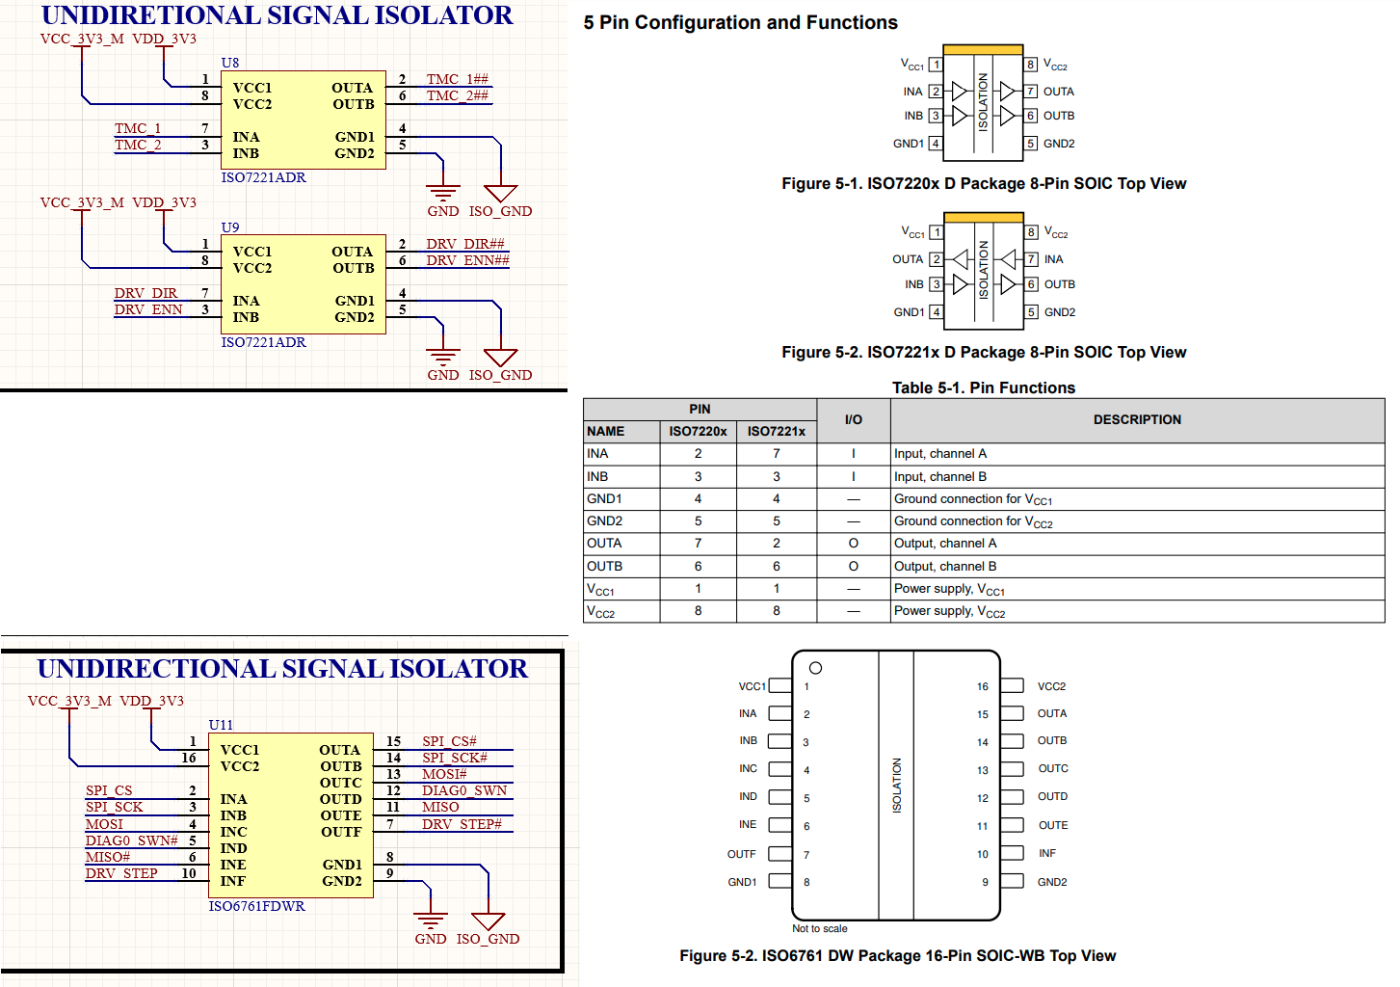
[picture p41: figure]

POINT NO. 5.

Isolator family should be upgraded to ISO77xx as recommended.

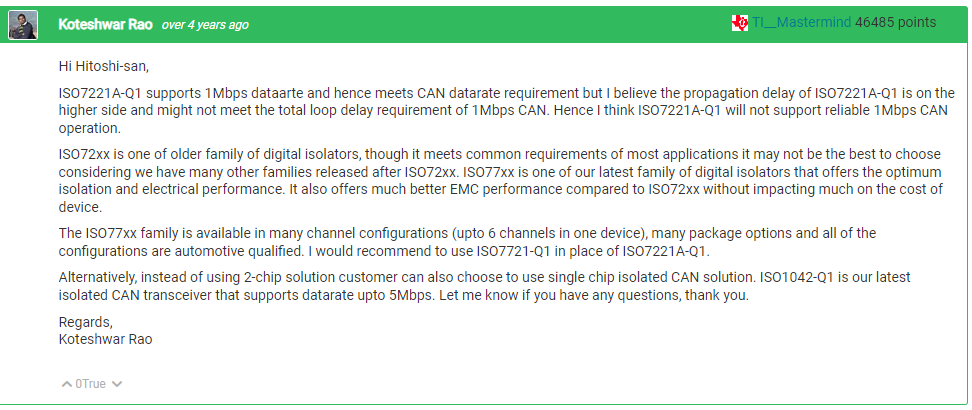
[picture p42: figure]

POINT NO. 6.

Observation on temperature Sensor PT100: The readings on net label TEMP_OUT were perfect and matched with the circuit formula. Observations can be checked here (https://drive.google.com/drive/folders/1N1xB0ozvQ0e6G91vdsShQJjVPCLtAHLW?usp=sharing).

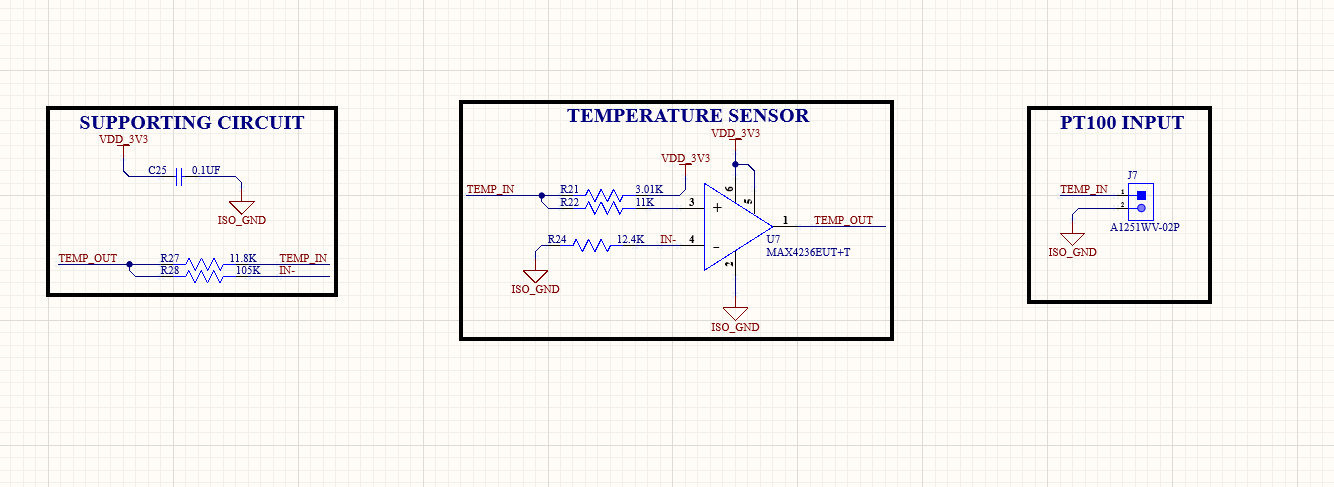
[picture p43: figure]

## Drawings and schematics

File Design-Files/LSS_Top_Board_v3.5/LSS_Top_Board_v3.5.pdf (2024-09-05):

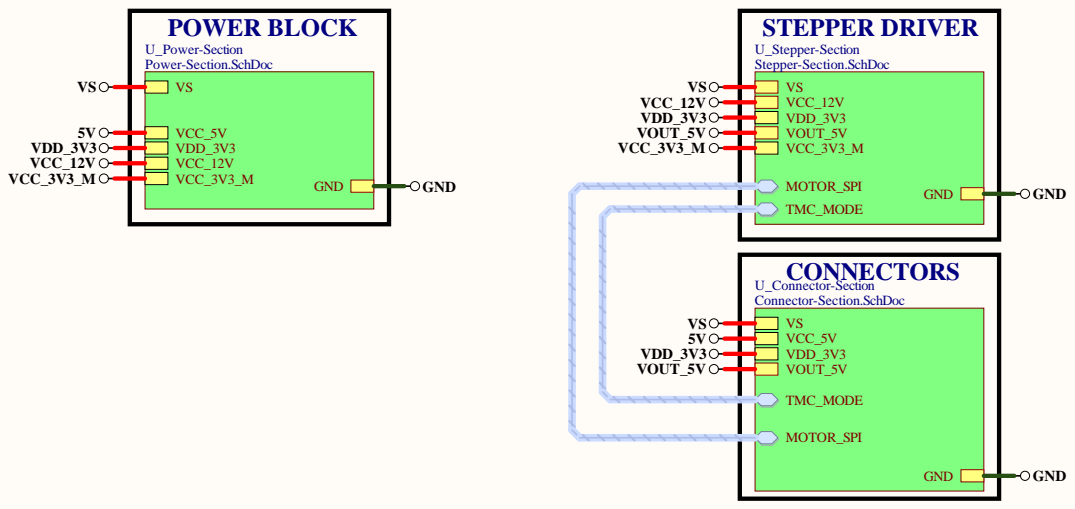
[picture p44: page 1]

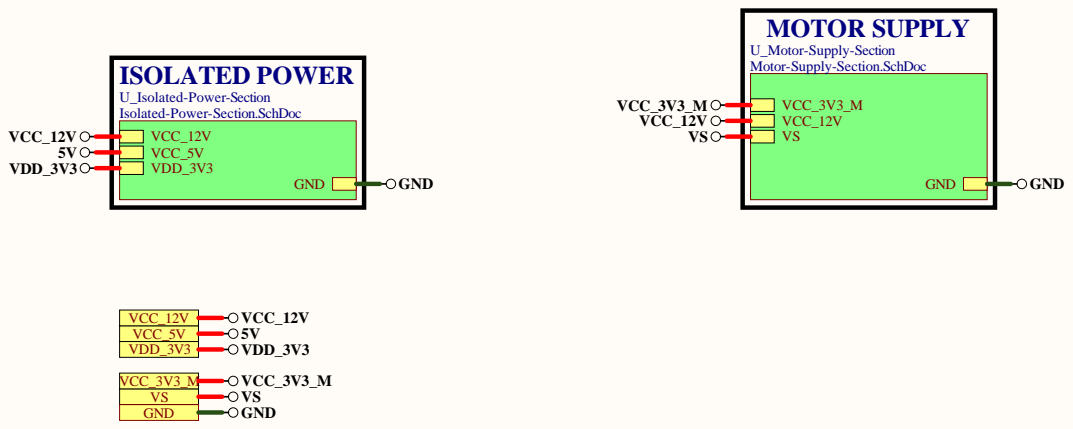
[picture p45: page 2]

U_Motor-Supply-Section
Motor-Supply-Section.SchDoc

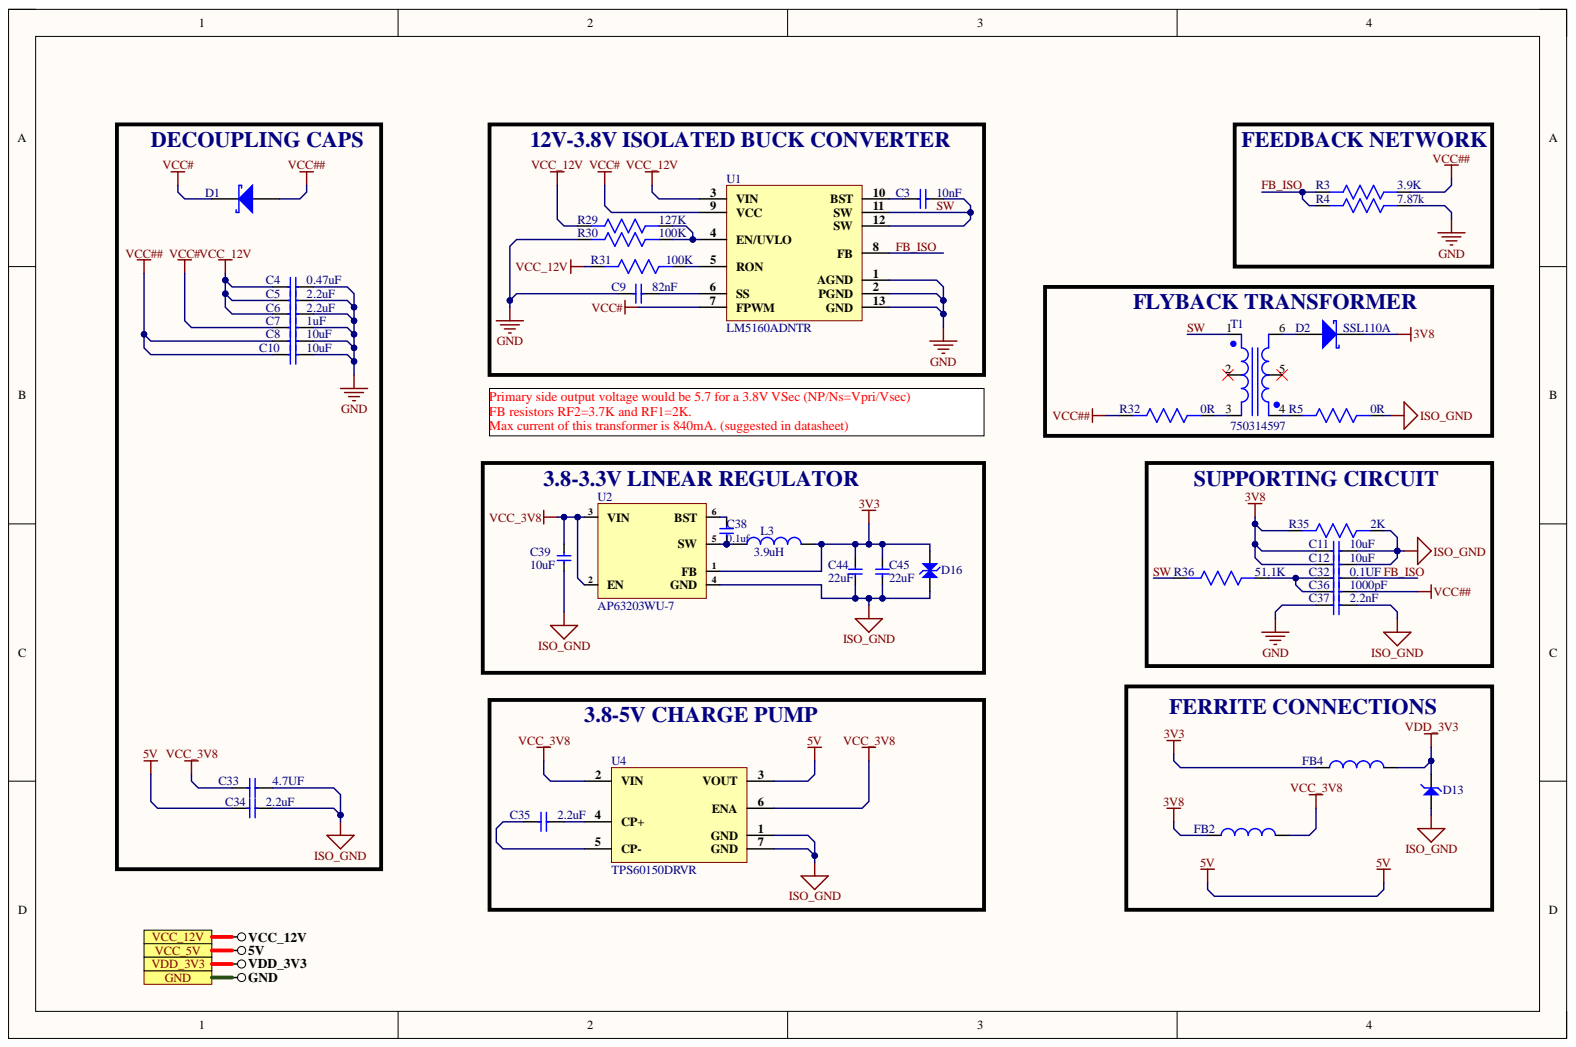
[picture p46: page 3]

Primary side output voltage would be 5.7 for a 3.8V VSec (NP/Ns=Vpri/Vsec)
FB resistors RF2=3.7K and RF1=2K.

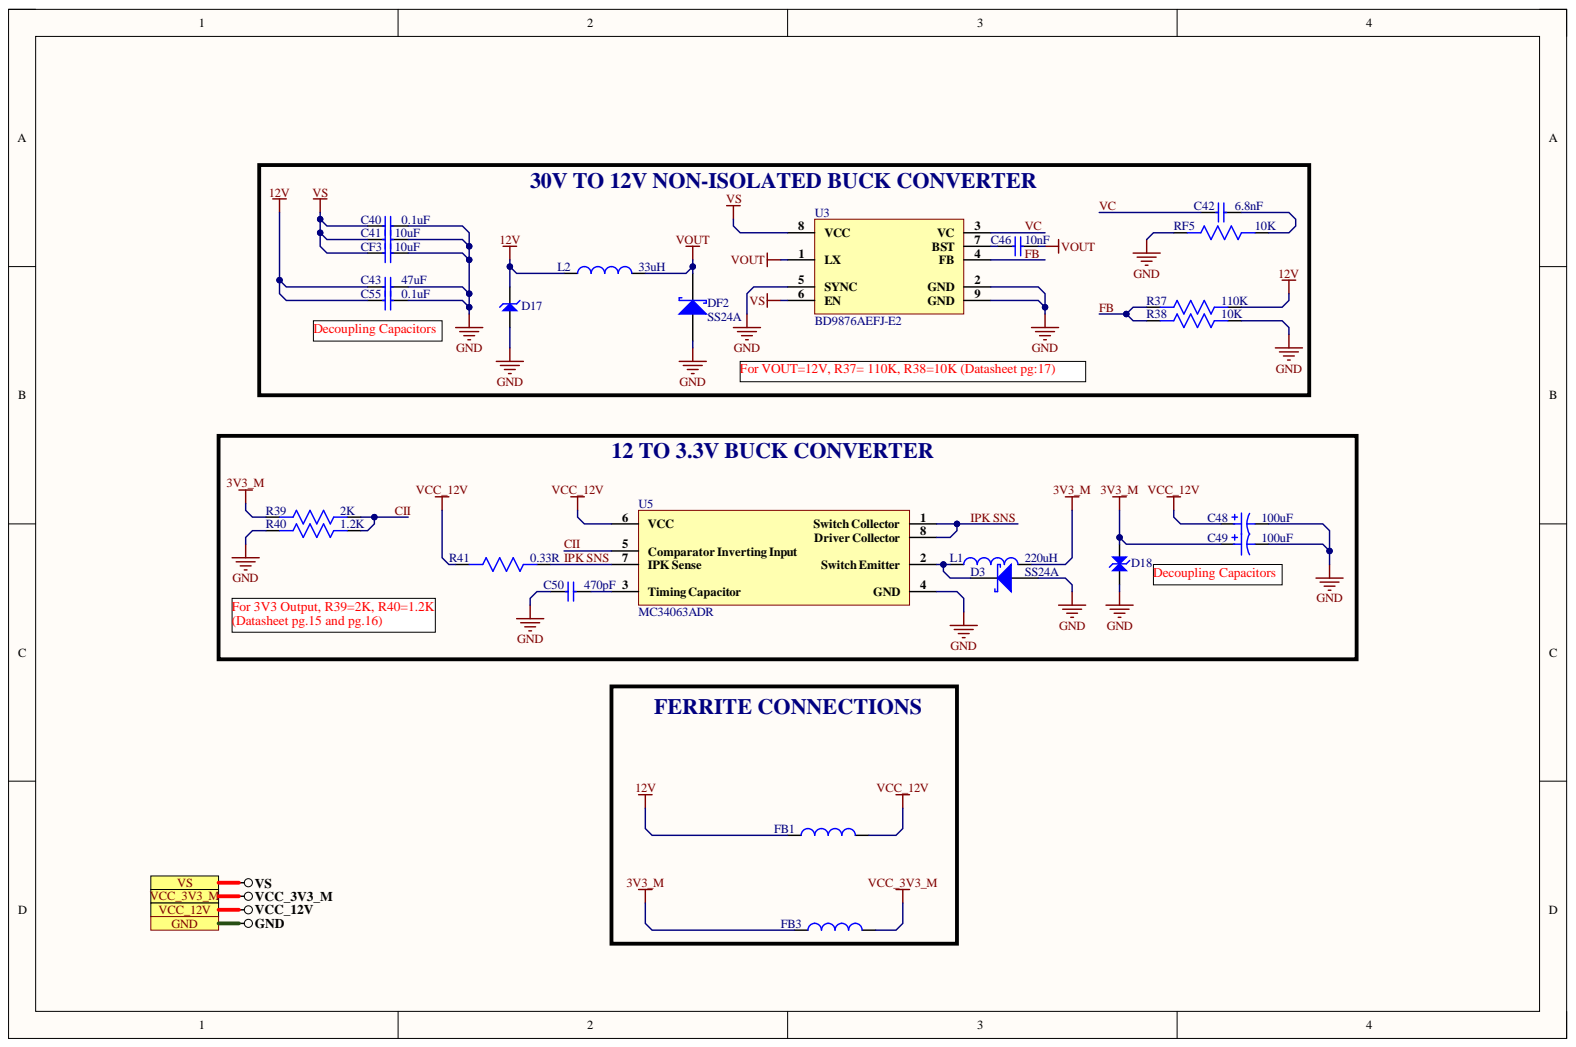
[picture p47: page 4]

30V TO 12V NON-ISOLATED BUCK CONVERTER

For VOUT=12V, R37= 110K, R38=10K (Datasheet pg:17)

For 3V3 Output, R39=2K, R40=1.2K
(Datasheet pg.15 and pg.16)

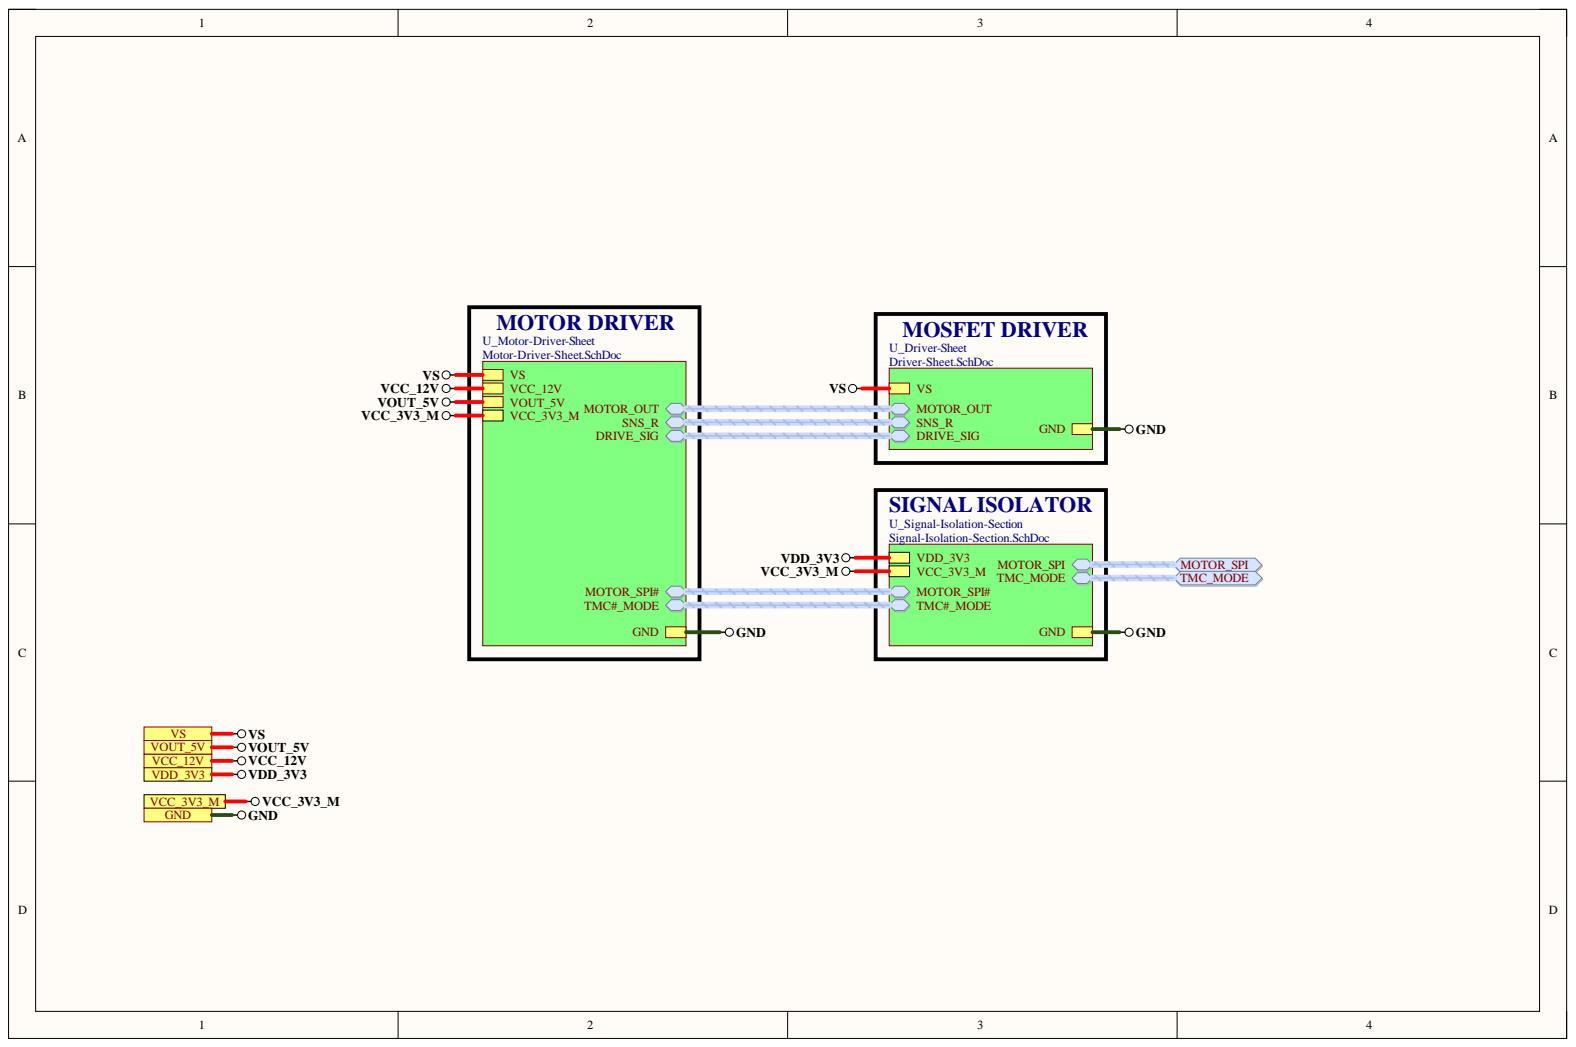
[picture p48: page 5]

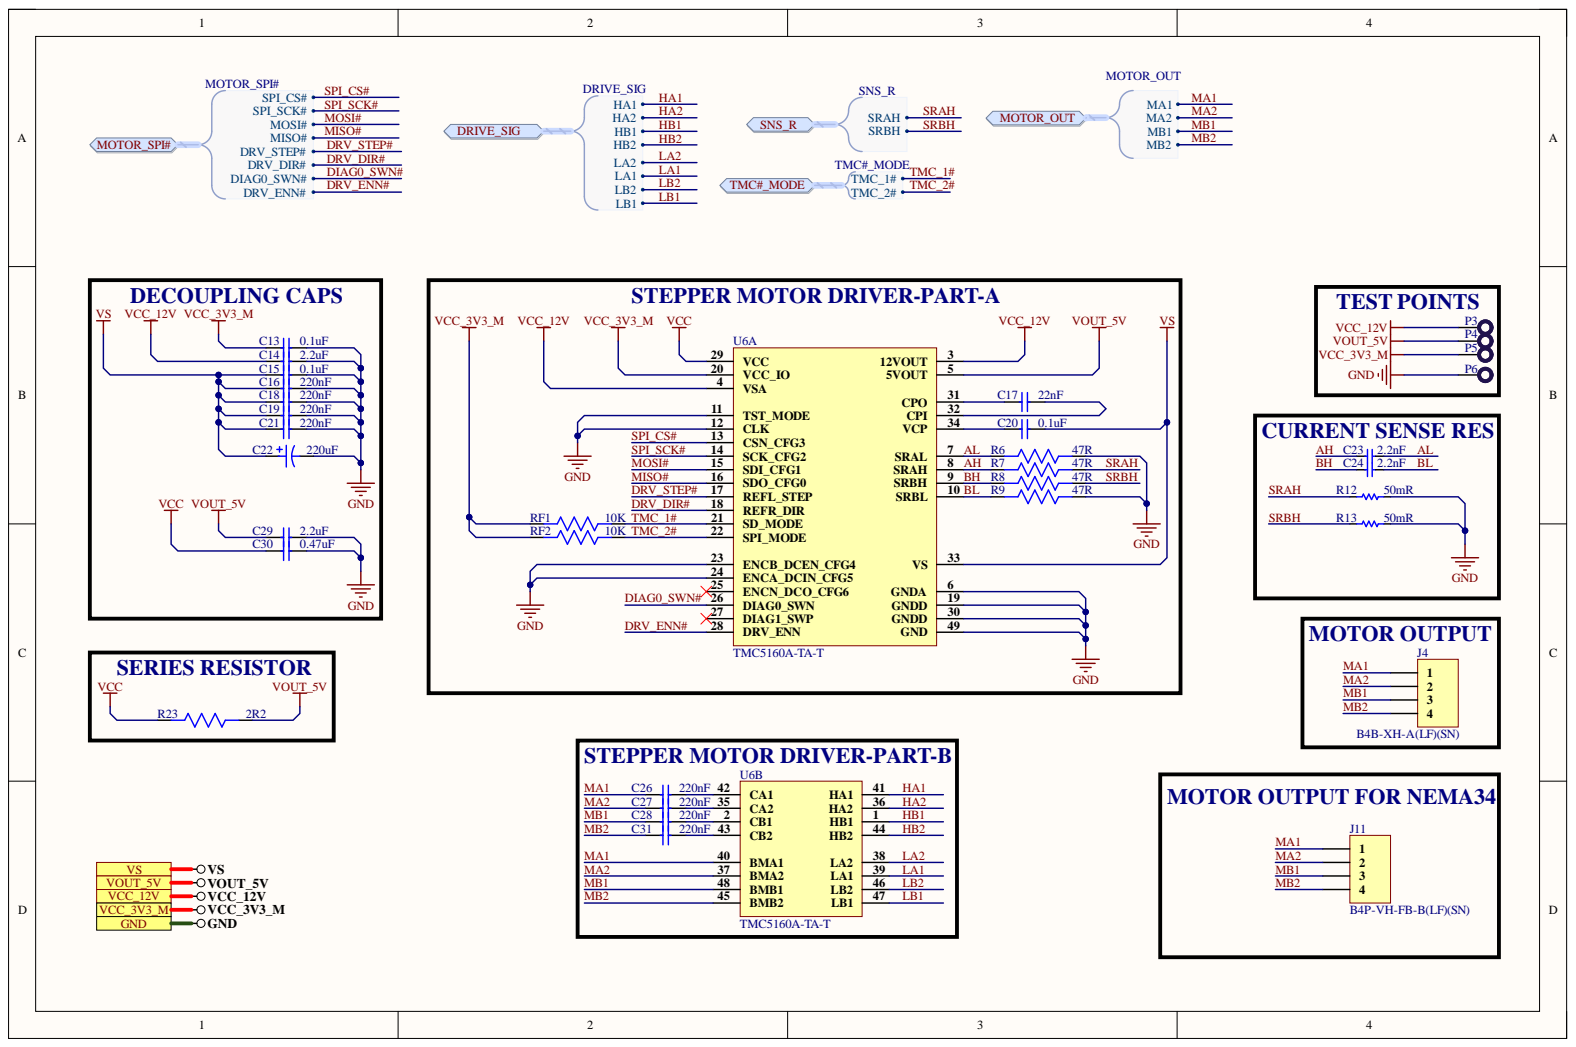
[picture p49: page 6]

MOTOR_SPI# | SPI_CS# | MOTOR_OUT DRIVE_SIG SNS_R HA1 LB1

STEPPER MOTOR DRIVER-PART-A

TEST POINTS

STEPPER MOTOR DRIVER-PART-B

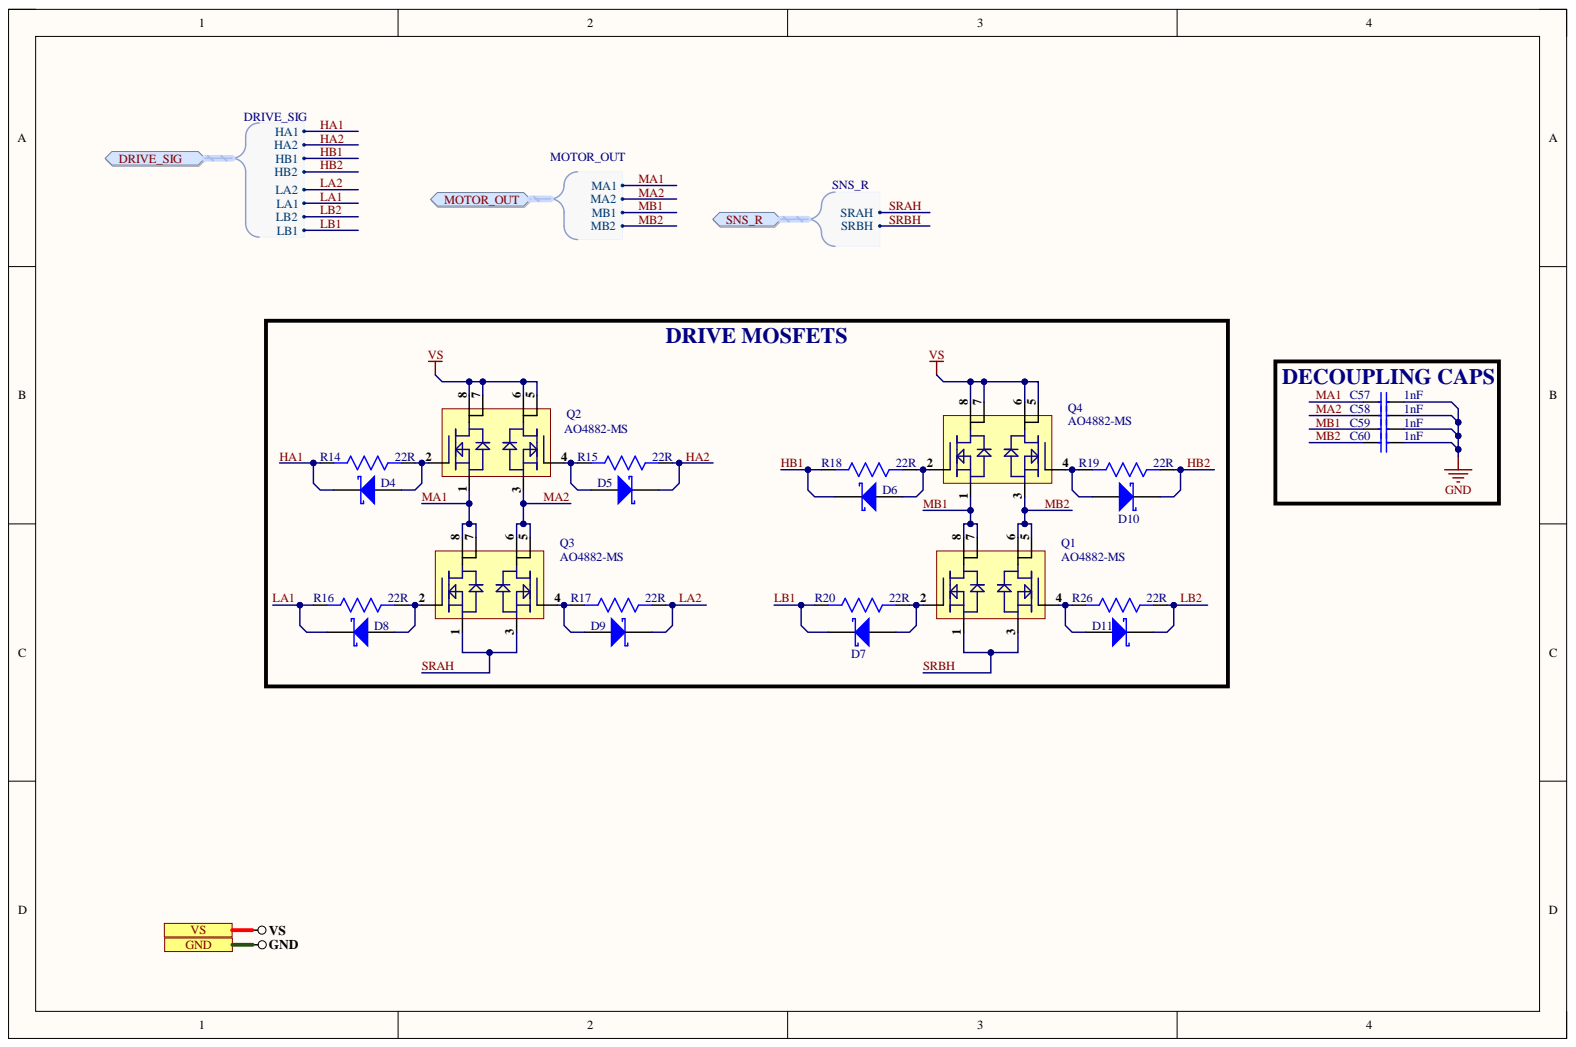
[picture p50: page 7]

DRIVE_SIG HA1 HA1 HB1 HB1 MOTOR_OUT LB1

VS | | DRIVE MOSFETS VS

DECOUPLING CAPS | GND

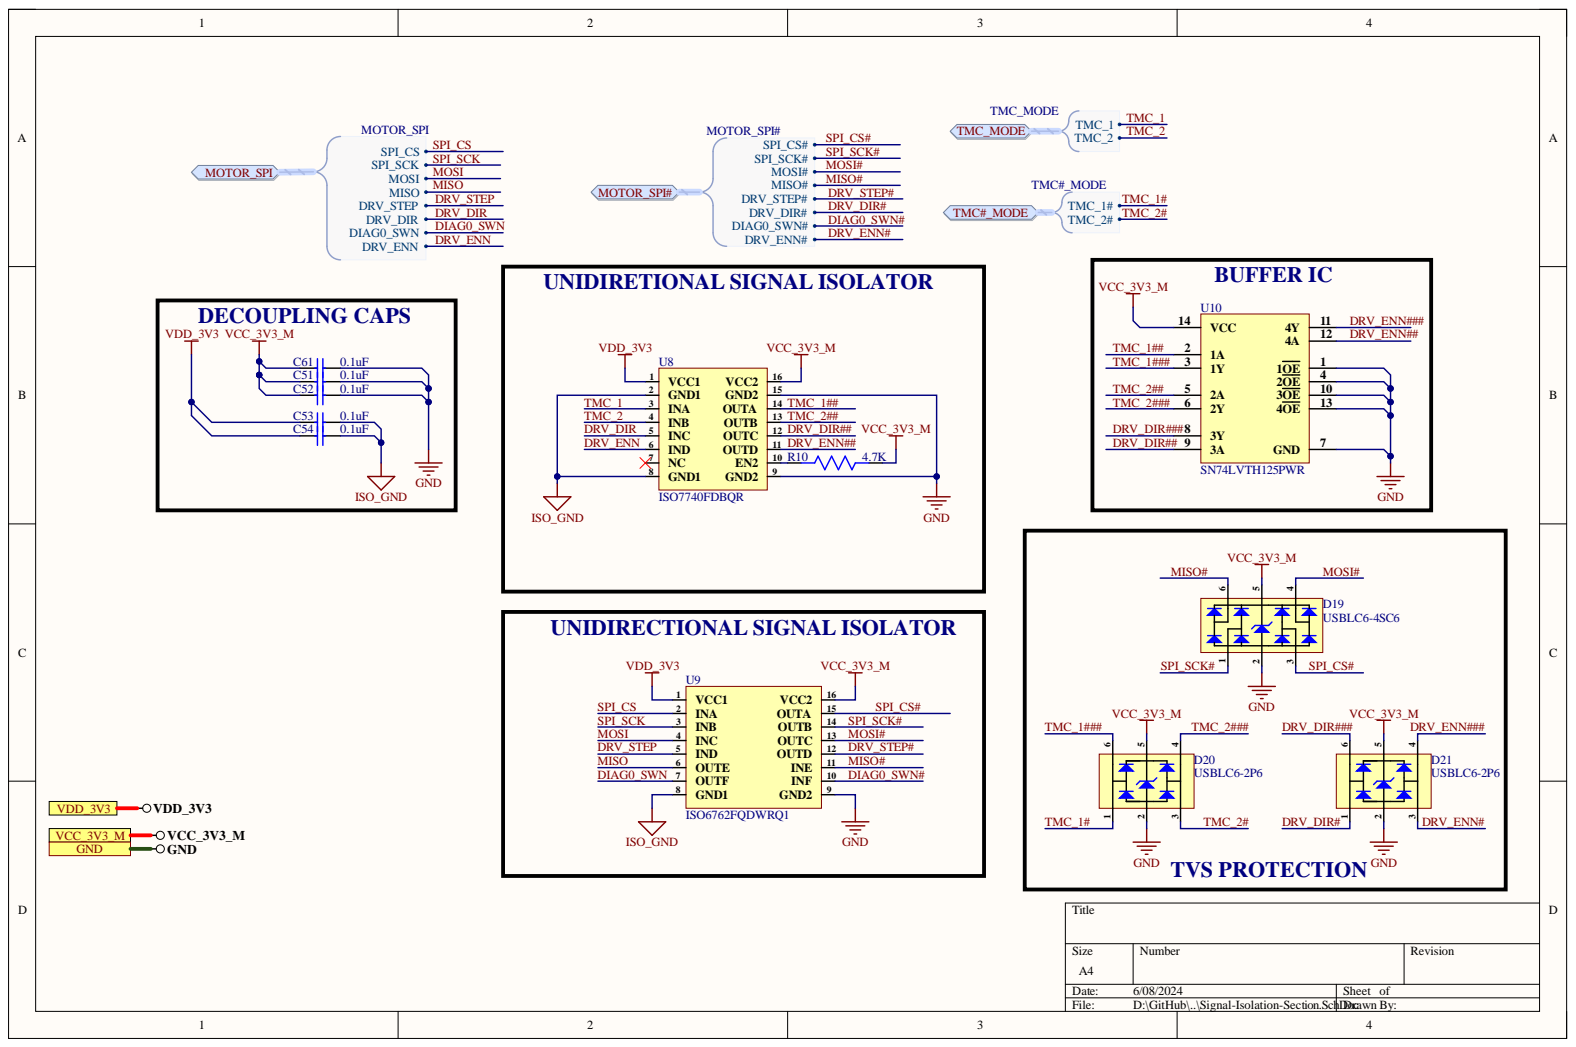
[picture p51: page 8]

Size A4 | Number | Revision

Date: 6/08/2024 | Sheet of
File: D:\GitHub\..\Signal-Isolation-Section.SchDDrocawn By:

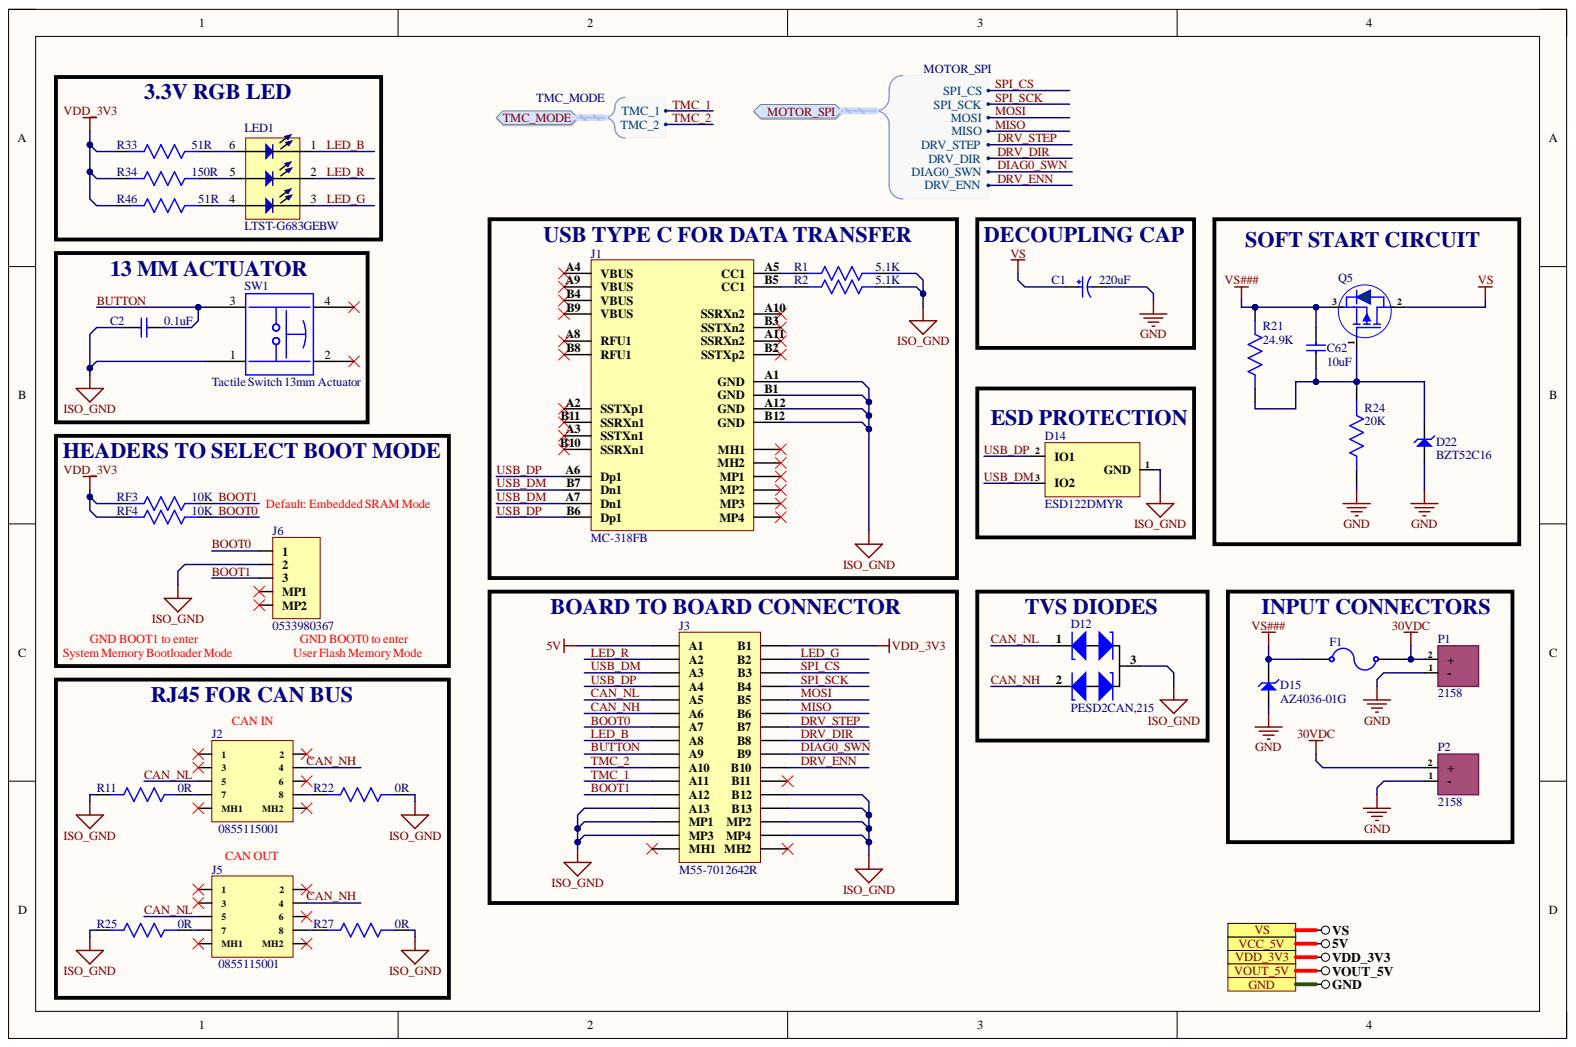
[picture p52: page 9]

USB TYPE C FOR DATA TRANSFER

HEADERS TO SELECT BOOT MODE

Default: Embedded SRAM Mode

BOARD TO BOARD CONNECTOR

GND BOOT1 to enter
System Memory Bootloader Mode

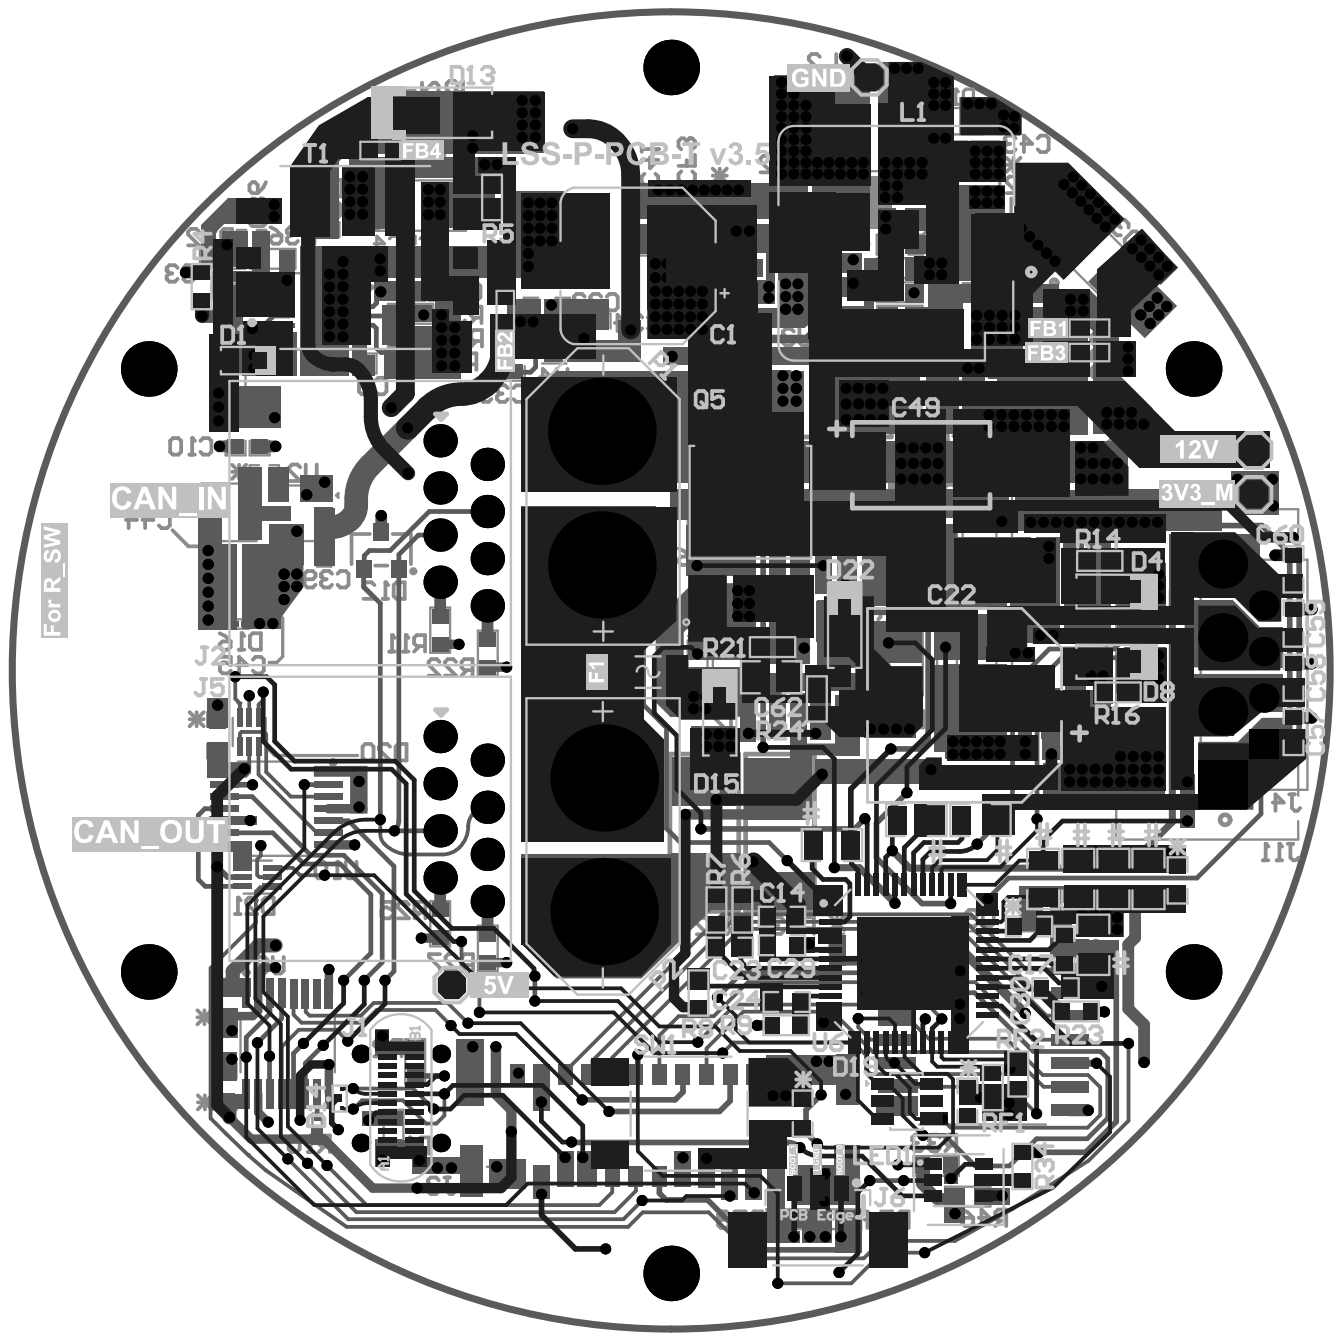
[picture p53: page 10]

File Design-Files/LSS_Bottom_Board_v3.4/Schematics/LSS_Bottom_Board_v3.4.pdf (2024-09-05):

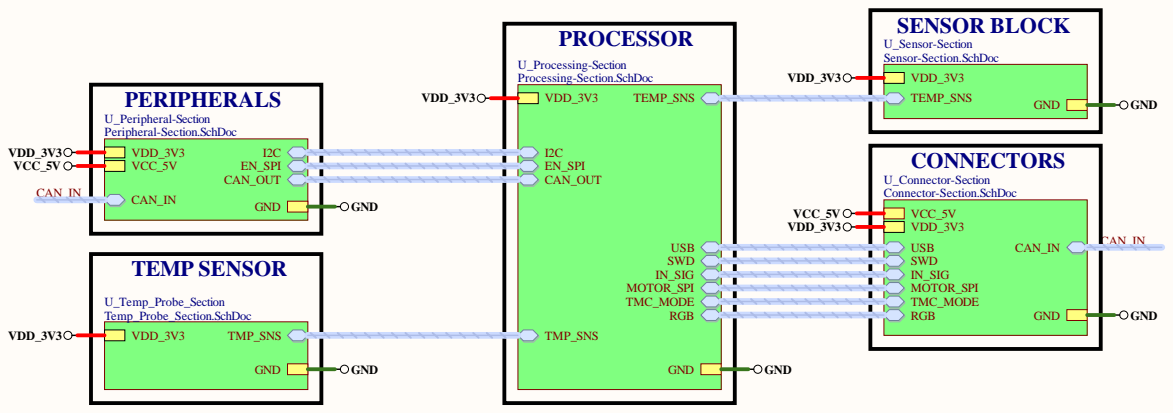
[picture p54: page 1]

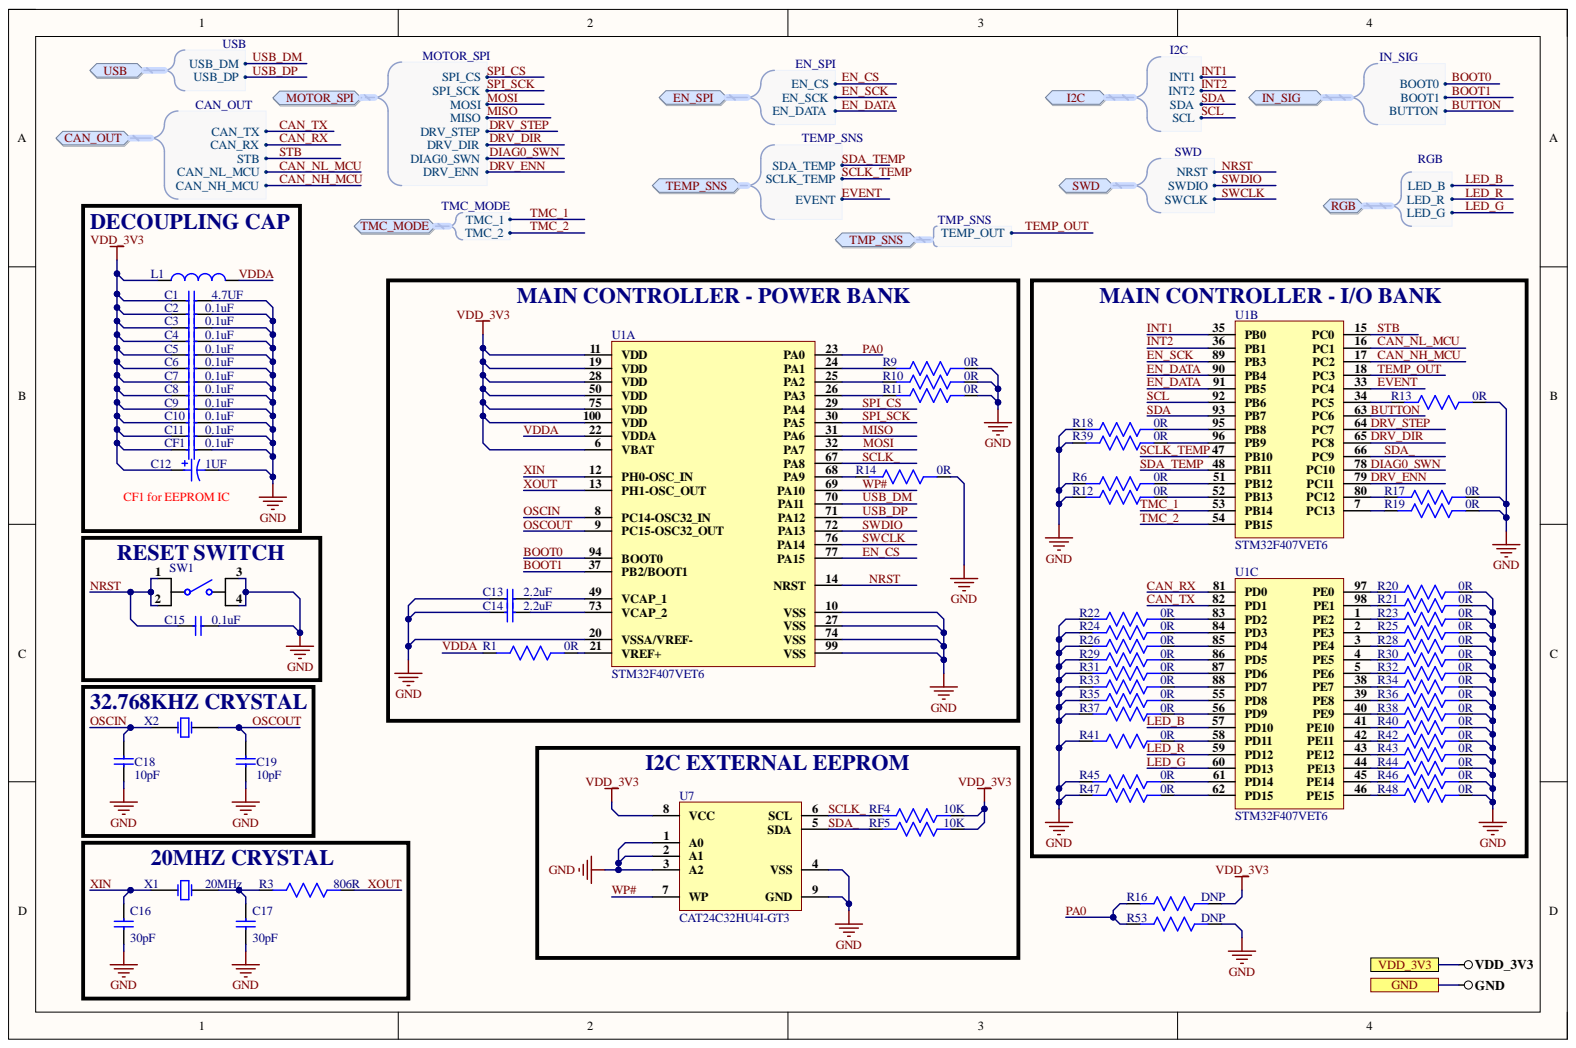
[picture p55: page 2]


U_Motion-Sensor-Sheet
Motion-Sensor-Sheet.SchDoc




Connections for CAN are w.r.t Controller Rx and Tx

RPULL AND SOLDER BRIDGE




BOARD TO BOARD CONNECTOR

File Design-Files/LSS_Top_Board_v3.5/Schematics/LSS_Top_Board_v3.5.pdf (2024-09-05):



U_Motor-Supply-Section
Motor-Supply-Section.SchDoc


Primary side output voltage would be 5.7 for a 3.8V VSec (NP/Ns=Vpri/Vsec)
FB resistors RF2=3.7K and RF1=2K.


30V TO 12V NON-ISOLATED BUCK CONVERTER

For VOUT=12V, R37= 110K, R38=10K (Datasheet pg:17)

For 3V3 Output, R39=2K, R40=1.2K
(Datasheet pg.15 and pg.16)



MOTOR_SPI# | SPI_CS# | MOTOR_OUT DRIVE_SIG SNS_R HA1 LB1

STEPPER MOTOR DRIVER-PART-A

TEST POINTS

STEPPER MOTOR DRIVER-PART-B


DRIVE_SIG HA1 HA1 HB1 HB1 MOTOR_OUT LB1

VS | | DRIVE MOSFETS VS

DECOUPLING CAPS


Size A4 | Number | Revision

Date: 6/06/2024 | Sheet of
File: C:\Users\..\Signal-Isolation-Section.SchDoDr c awn By:


USB TYPE C FOR DATA TRANSFER

HEADERS TO SELECT BOOT MODE

Default: Embedded SRAM Mode

BOARD TO BOARD CONNECTOR

GND BOOT1 to enter
System Memory Bootloader Mode













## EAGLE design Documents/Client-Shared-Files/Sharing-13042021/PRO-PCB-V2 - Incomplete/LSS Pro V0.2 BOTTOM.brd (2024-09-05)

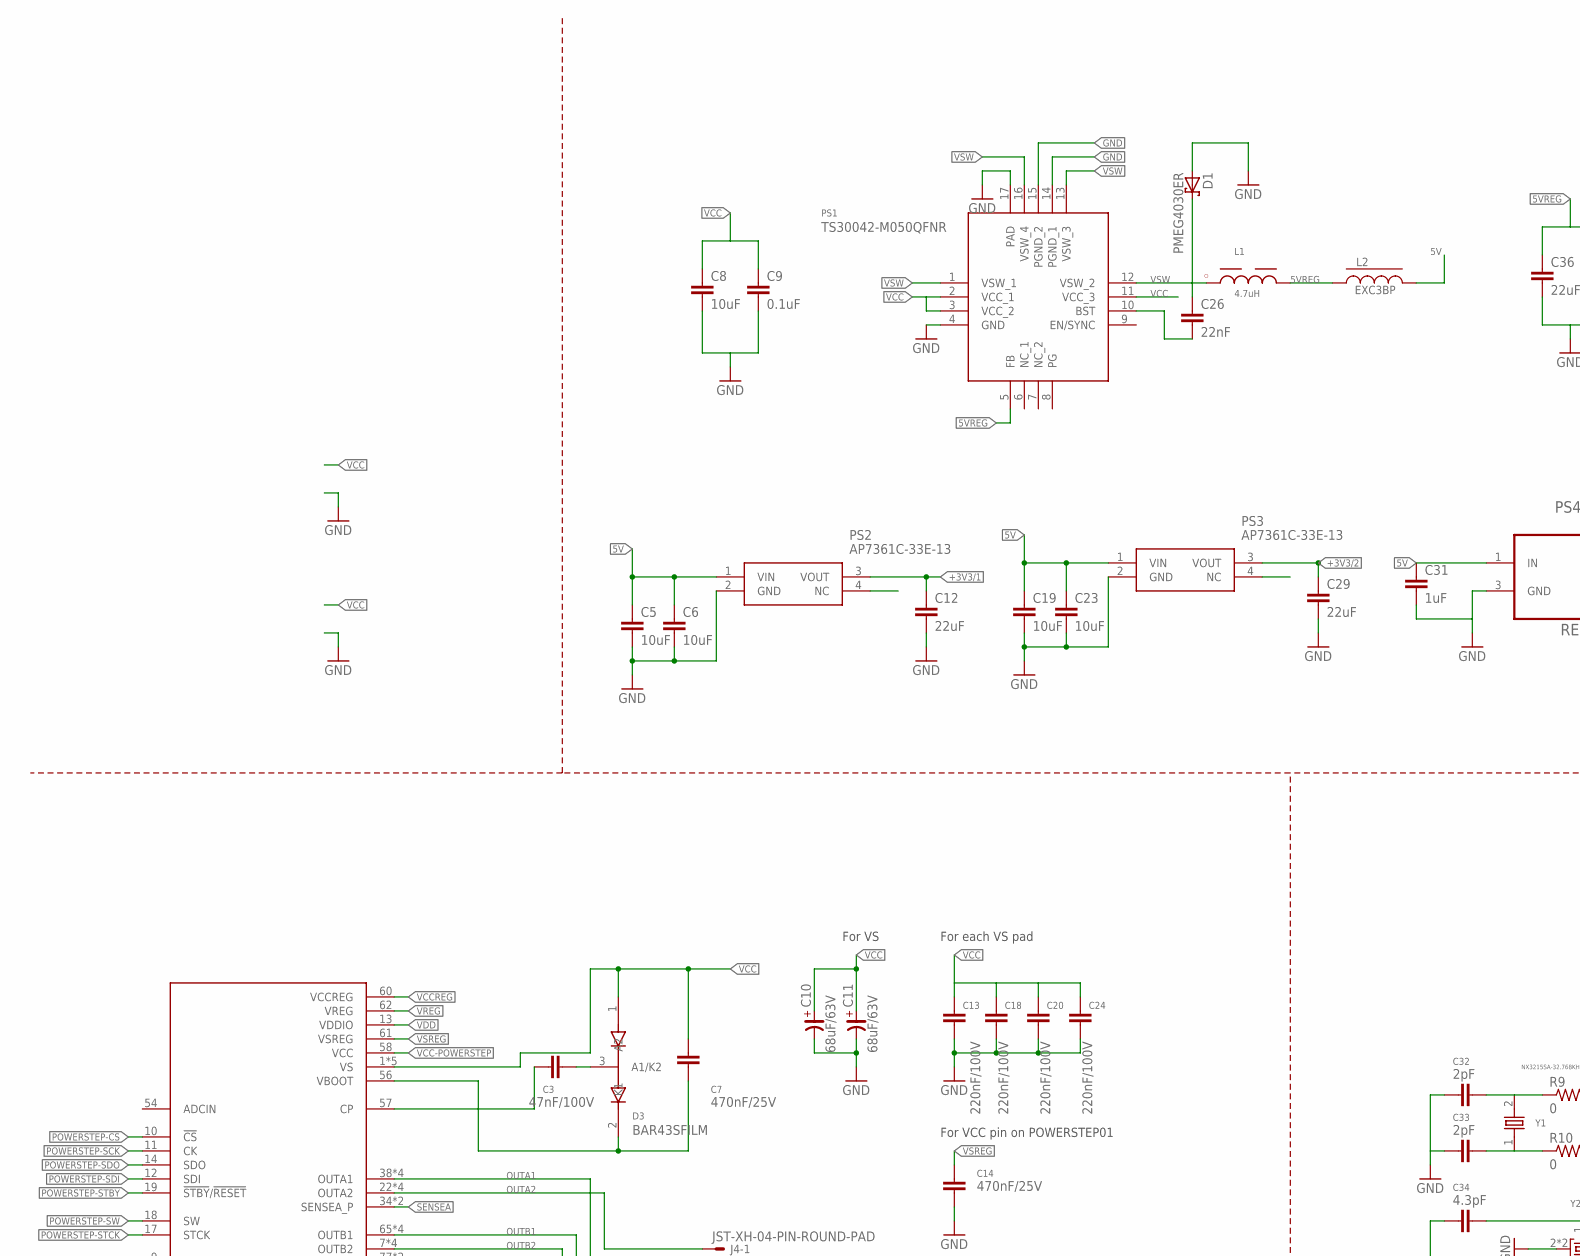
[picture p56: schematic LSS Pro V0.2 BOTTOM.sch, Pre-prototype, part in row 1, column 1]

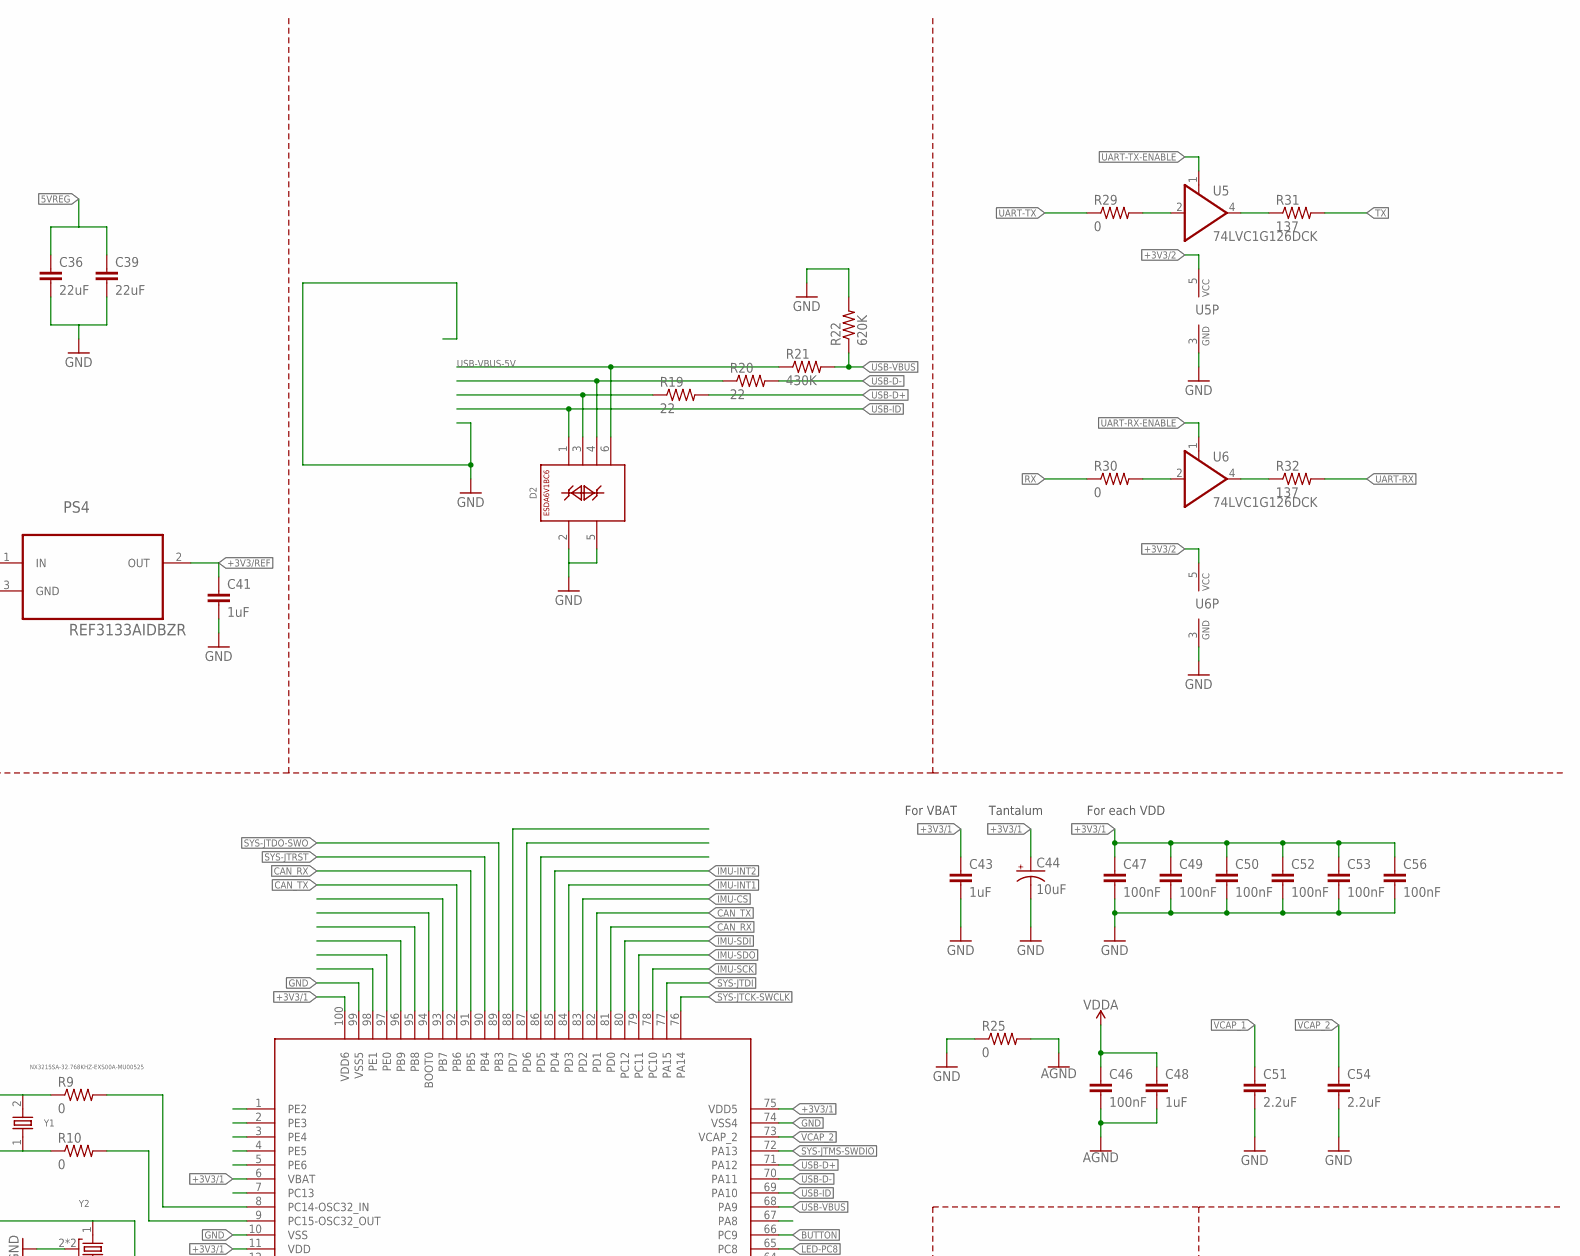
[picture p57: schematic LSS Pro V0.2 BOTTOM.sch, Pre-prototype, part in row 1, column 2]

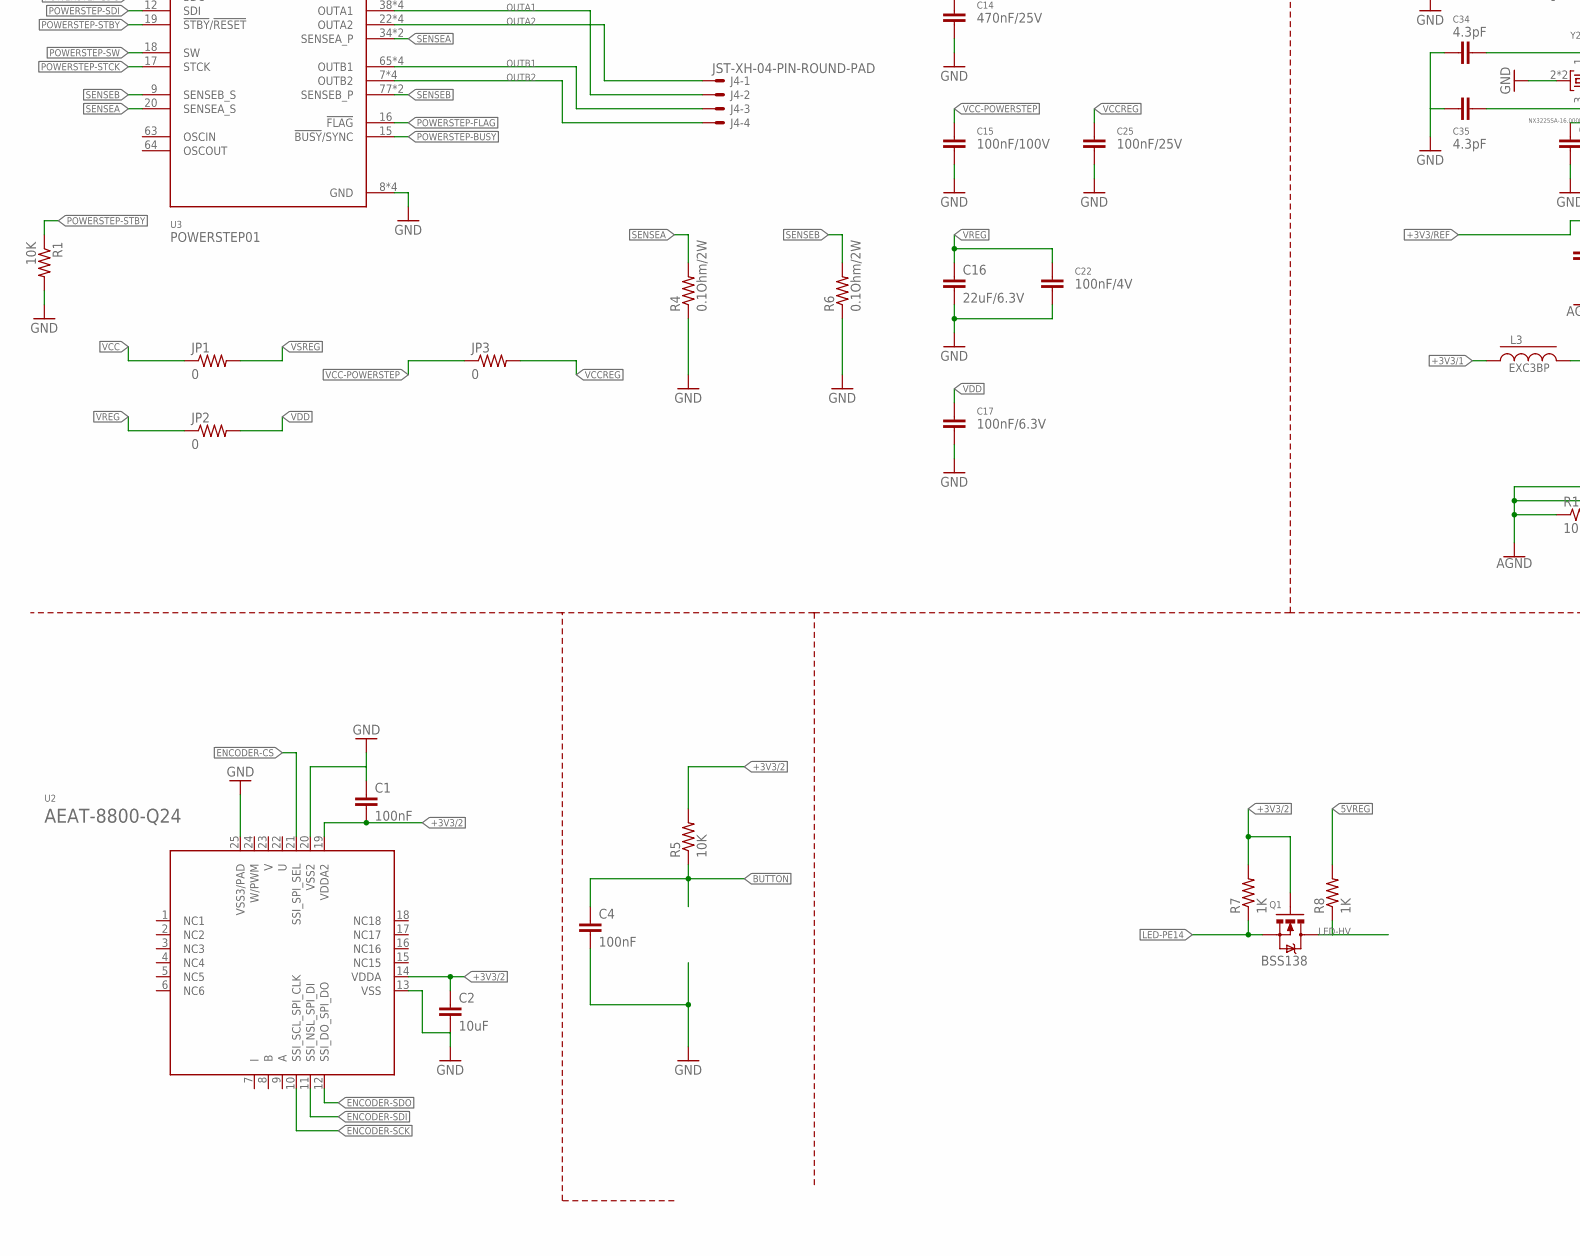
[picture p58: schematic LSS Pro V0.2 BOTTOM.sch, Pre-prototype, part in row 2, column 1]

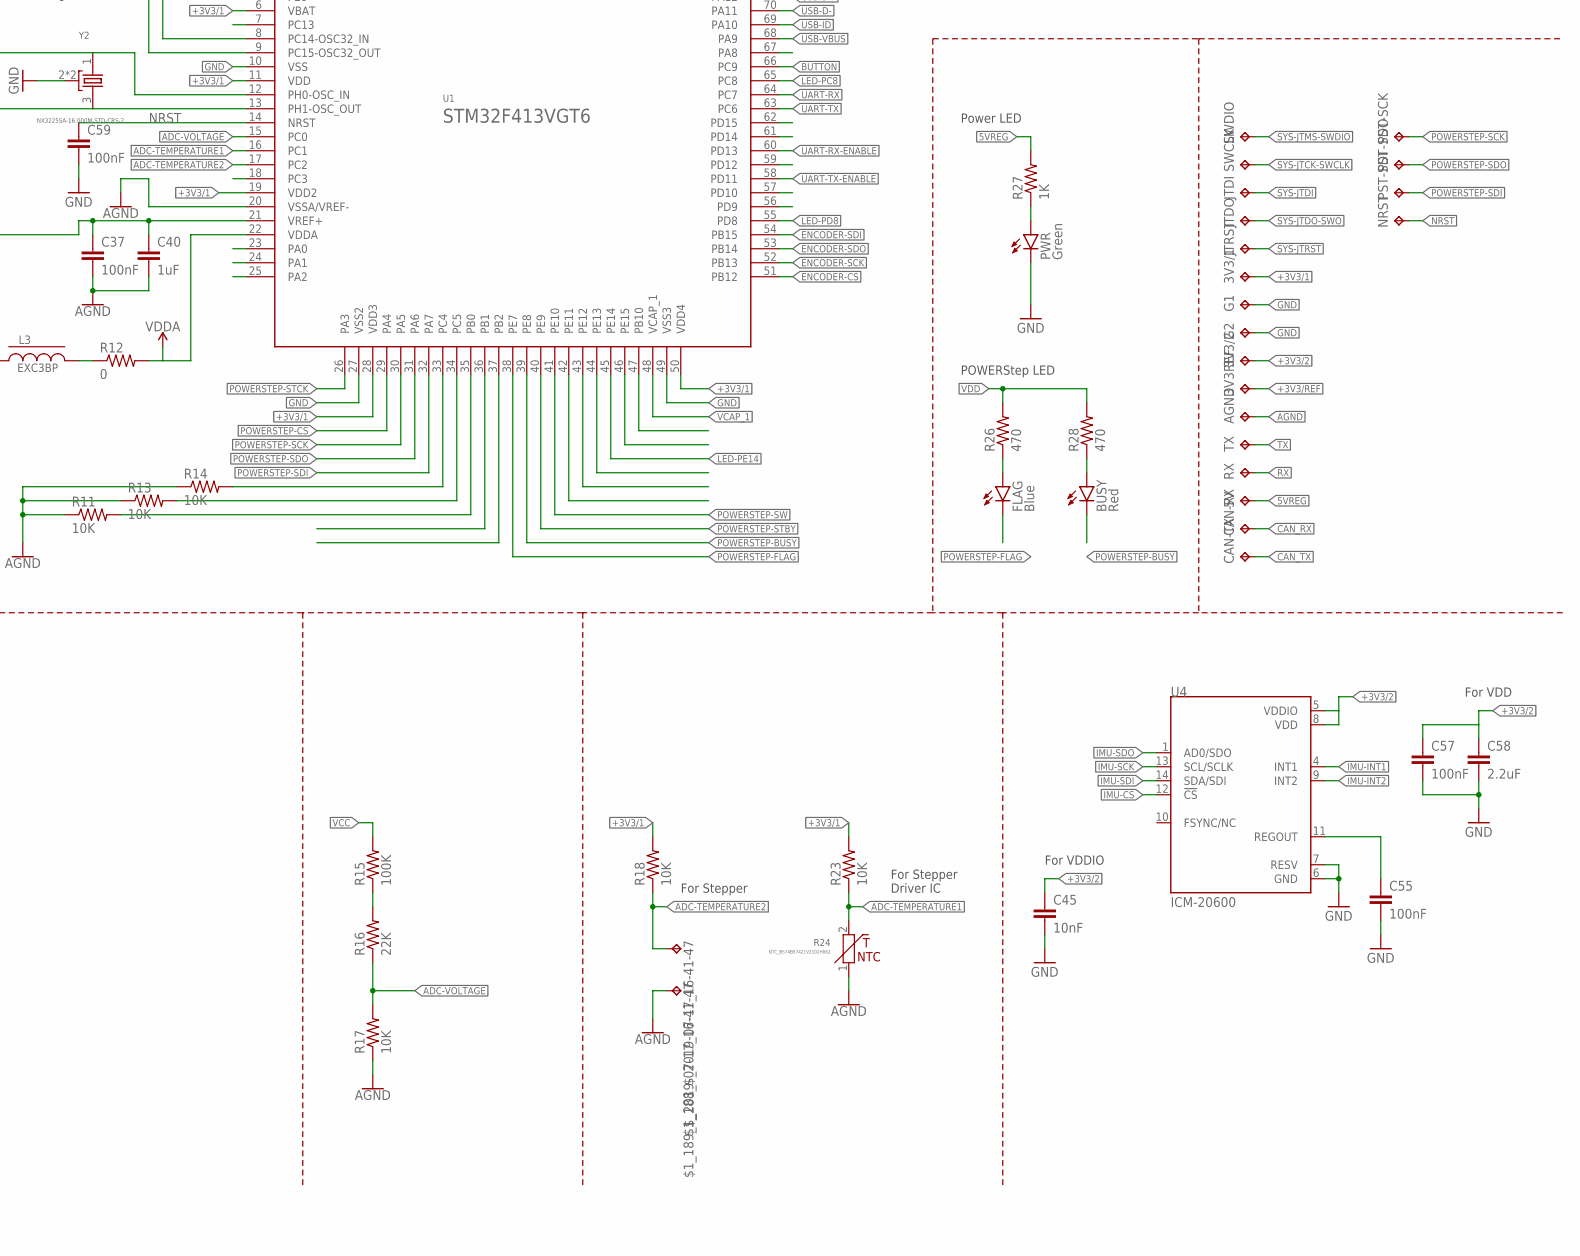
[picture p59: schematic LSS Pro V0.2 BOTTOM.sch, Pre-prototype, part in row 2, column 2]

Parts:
3V3/1, 3V3/2, 3V3REF, 5V: TPTP17R; TP17R
$1_188_$_2019-07-17_16-41-47, $1_189_$_2019-07-17_16-41-47: TP-040
AGND: TPTP17R; TP17R
BUSY: Red; LED-0603
C1, C4, C37, C46, C47, C49, C50, C52, C53, C55, C56, C57, C59: 100nF; 0603-CAP
C2: 10uF; 0603-CAP
C3: 47nF/100V; 0805
C5, C6, C19, C23: 10uF; 0805
C7, C14: 470nF/25V; 0603-CAP
C8: 10uF; 1206
C9: 0.1uF; 0603-CAP
C10, C11: 68uF/63V; CSV-E/F
C12, C29, C36, C39: 22uF; 0805
C13, C18, C20, C24: 220nF/100V; 0805
C15: 100nF/100V; 0603-CAP
C16: 22uF/6.3V; 1206
C17: 100nF/6.3V; 0603-CAP
C22: 100nF/4V; 0603-CAP
C25: 100nF/25V; 0603-CAP
C26: 22nF; 0402-CAP
C31, C41: 1uF; 0805
C32, C33: 2pF; 0603-CAP
C34, C35: 4.3pF; 0603-CAP
C40, C43, C48: 1uF; 0603-CAP
C44: 10uF; EIA3216
C45: 10nF; 0603-CAP
C51, C54, C58: 2.2uF; 1206
CAN-RX: TPTP17R; TP17R
CAN-TX: TPTP17R; TP17R
D1: PMEG4030ER; SOD123W
D2: ESDA6V1BC6; SOT-23-6L
D3: BAR43SFILM; SOT105P242X150-3N
FLAG: Blue; LED-0603
G1, G2: TPTP17R; TP17R
J4: JST-XH-04-PIN-ROUND-PAD; JST-XH-04-PACKAGE-ROUND-PAD
JP1, JP2, JP3: 0; 0603-RES
JTDI: TPTP17R; TP17R
JTDO: TPTP17R; TP17R
JTRST: TPTP17R; TP17R
L1: 4.7uH; WE-PD2_5848/5820
L2, L3: EXC3BP; L0603
NRST: TPTP17R; TP17R
PS1: TS30042-M050QFNR; QFN16
PS2, PS3: AP7361C-33E-13; SOT230P700X165-4N
PS4: REF3133AIDBZR; SOT95P237X112-3N
PST-SCK: TPTP17R; TP17R
PST-SDI: TPTP17R; TP17R
PST-SDO: TPTP17R; TP17R
PWR: Green; LED-0603
Q1: BSS138; SOT23-3
R1, R11, R13, R14: 10K; 0402-RES
R4, R6: 0.1Ohm/2W; R2512
R5, R17, R18, R23: 10K; 0603-RES
R7, R8: 1K; 0603-RES
R9, R10, R12, R25, R29, R30: 0; 0603-RES
R15: 100K; 0603-RES
R16: 22K; 0603-RES
R19, R20: 22; 0603-RES
R21: 430K; 0603-RES
R22: 620K; 0603-RES
R24: NTC_B574B57421V2102H062; R0805
R26, R28: 470; 0402-RES
R27: 1K; 0402-RES
R31, R32: 137; 0603-RES
RX: TPTP17R; TP17R
SWCLK: TPTP17R; TP17R
SWDIO: TPTP17R; TP17R
TX: TPTP17R; TP17R
U1: STM32F413VGT6; LQFP100
U2: AEAT-8800-Q24; QFN24
U3: POWERSTEP01; IC_POWERSTEP01
U4: ICM-20600; PQFN50P250X300X97-14N
U5, U6: 74LVC1G126DCK; SC70-5
Y1: NX3215SA-32.768KHZ-EXS00A-MU00525; NX3215SA
Y2: NX3225SA-16.000M-STD-CRS-2; OSCCC320X250X60N

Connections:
5V: C5.1, C6.1, C19.1, C23.1, C31.1, L2.2, PS2.1 (VIN), PS3.1 (VIN), PS4.1 (IN)
5VREG: 5V.TP, C36.1, C39.1, L1.2, L2.1, PS1.5 (FB), R8.2, R27.2
+3V3/1: 3V3/1.TP, C12.1, C43.1, C44.A (+), C47.1, C49.1, C50.1, C52.1, C53.1, C56.1, L3.1, PS2.3 (VOUT), R18.2, R23.2, U1.6 (VBAT), U1.11 (VDD), U1.19 (VDD2), U1.28 (VDD3), U1.50 (VDD4), U1.75 (VDD5), U1.100 (VDD6)
+3V3/2: 3V3/2.TP, C1.2, C2.1, C29.1, C45.1, C57.1, C58.1, PS3.3 (VOUT), Q1.1 (G), R5.2, R7.2, U2.14 (VDDA), U2.19 (VDDA2), U4.5 (VDDIO), U4.8 (VDD), U5.5 (VCC), U6.5 (VCC)
+3V3/REF: 3V3REF.TP, C37.1, C40.1, C41.1, PS4.2 (OUT), U1.21 (VREF+)
ADC-TEMPERATURE1: R23.1, R24.2, U1.16 (PC1)
ADC-TEMPERATURE2: $1_188_$_2019-07-17_16-41-47.1, R18.1, U1.17 (PC2)
ADC-VOLTAGE: R16.1, R17.2, U1.15 (PC0)
AGND: $1_189_$_2019-07-17_16-41-47.1, AGND.TP, C37.2, C40.2, C46.2, C48.2, R11.1, R13.1, R14.1, R17.1, R24.1, R25.2, U1.20 (VSSA/VREF-)
BUTTON: C4.1, R5.1, U1.66 (PC9)
CAN_RX: CAN-RX.TP, U1.81 (PD0), U1.91 (PB5)
CAN_TX: CAN-TX.TP, U1.82 (PD1), U1.92 (PB6)
ENCODER-CS: U1.51 (PB12), U2.21 (SSI_SPI_SEL)
ENCODER-SCK: U1.52 (PB13), U2.10 (SSI_SCL_SPI_CLK)
ENCODER-SDI: U1.54 (PB15), U2.11 (SSI_NSL_SPI_DI)
ENCODER-SDO: U1.53 (PB14), U2.12 (SSI_DO_SPI_DO)
GND: C1.1, C2.2, C4.2, C5.2, C6.2, C8.2, C9.2, C10.-, C11.-, C12.2, C13.2, C14.2, C15.2, C16.2, C17.2, C18.2, C19.2, C20.2, C22.2, C23.2, C24.2, C25.2, C29.2, C31.2, C32.2, C33.2, C34.2, C35.2, C36.2, C39.2, C41.2, C43.2, C44.C (-), C45.2, C47.2, C49.2, C50.2, C51.2, C52.2, C53.2, C54.2, C55.2, C56.2, C57.2, C58.2, C59.2, D1.2 (A), D2.2, D2.5, G1.TP, G2.TP, PS1.4 (GND), PS1.14 (PGND_1), PS1.15 (PGND_2), PS1.17 (PAD), PS2.2 (GND), PS3.2 (GND), PS4.3 (GND), PWR.C, R1.2, R4.1, R6.1, R22.2, R25.1, U1.10 (VSS), U1.27 (VSS2), U1.49 (VSS3), U1.74 (VSS4), U1.99 (VSS5), U2.13 (VSS), U2.20 (VSS2), U2.25 (VSS3/PAD), U3.8 (GND), U3.21 (GND), U3.59 (GND), U3.EPAD9 (GND), U4.6 (GND), U4.7 (RESV), U5.3 (GND), U6.3 (GND), Y2.2 (GND), Y2.4 (GND)
IMU-CS: U1.83 (PD2), U4.12 (!CS)
IMU-INT1: U1.84 (PD3), U4.4 (INT1)
IMU-INT2: U1.85 (PD4), U4.9 (INT2)
IMU-SCK: U1.78 (PC10), U4.13 (SCL/SCLK)
IMU-SDI: U1.80 (PC12), U4.14 (SDA/SDI)
IMU-SDO: U1.79 (PC11), U4.1 (AD0/SDO)
LED-HV: Q1.3 (D), R8.1
LED-PC8: U1.65 (PC8)
LED-PD8: U1.55 (PD8)
LED-PE14: Q1.2 (S), R7.1, U1.45 (PE14)
unnamed: R30.2, U6.2 (I)
unnamed: R9.2, U1.8 (PC14-OSC32_IN)
unnamed: R10.2, U1.9 (PC15-OSC32_OUT)
unnamed: L3.2, R12.1
unnamed: R32.1, U6.4 (O)
unnamed: C34.1, U1.12 (PH0-OSC_IN), Y2.1
unnamed: C35.1, U1.13 (PH1-OSC_OUT), Y2.3
unnamed: PWR.A, R27.1
unnamed: R29.2, U5.2 (I)
unnamed: R31.1, U5.4 (O)
unnamed: C32.1, R9.1, Y1.2
unnamed: C33.1, R10.1, Y1.1
unnamed: FLAG.A, R26.1
unnamed: C3.1, U3.57 (CP)
unnamed: R15.1, R16.2
unnamed: C55.1, U4.11 (REGOUT)
unnamed: BUSY.A, R28.1
unnamed: D2.4, R20.1
unnamed: D2.3, R19.1
unnamed: C3.2, D3.3 (A1/K2)
unnamed: R14.2, U1.33 (PC4)
unnamed: R13.2, U1.34 (PC5)
unnamed: R11.2, U1.35 (PB0)
unnamed: C7.2, D3.2 (K1), U3.56 (VBOOT)
unnamed: C26.2, PS1.10 (BST)
NRST: C59.1, NRST.TP, U1.14 (NRST)
OUTA1: J4.2, U3.38 (OUTA1), U3.42 (OUTA1), U3.53 (OUTA1), U3.EPAD4 (OUTA1)
OUTA2: J4.1, U3.22 (OUTA2), U3.33 (OUTA2), U3.37 (OUTA2), U3.EPAD3 (OUTA2)
OUTB1: J4.3, U3.65 (OUTB1), U3.76 (OUTB1), U3.80 (OUTB1), U3.EPAD7 (OUTB1)
OUTB2: J4.4, U3.7 (OUTB2), U3.81 (OUTB2), U3.85 (OUTB2), U3.EPAD8 (OUTB2)
POWERSTEP-BUSY: BUSY.C, U1.39 (PE8), U3.15 (!BUSY!/SYNC)
POWERSTEP-CS: U1.29 (PA4), U3.10 (!CS)
POWERSTEP-FLAG: FLAG.C, U1.38 (PE7), U3.16 (!FLAG)
POWERSTEP-SCK: PST-SCK.TP, U1.30 (PA5), U3.11 (CK)
POWERSTEP-SDI: PST-SDI.TP, U1.32 (PA7), U3.12 (SDI)
POWERSTEP-SDO: PST-SDO.TP, U1.31 (PA6), U3.14 (SDO)
POWERSTEP-STBY: R1.1, U1.40 (PE9), U3.19 (!STBY!/!RESET)
POWERSTEP-STCK: U1.26 (PA3), U3.17 (STCK)
POWERSTEP-SW: U1.41 (PE10), U3.18 (SW)
RX: R30.1, RX.TP
SENSEA: R4.2, U3.20 (SENSEA_S), U3.34 (SENSEA_P), U3.39 (SENSEA_P)
SENSEB: R6.2, U3.9 (SENSEB_S), U3.77 (SENSEB_P), U3.82 (SENSEB_P)
SYS-JTCK-SWCLK: SWCLK.TP, U1.76 (PA14)
SYS-JTDI: JTDI.TP, U1.77 (PA15)
SYS-JTDO-SWO: JTDO.TP, U1.89 (PB3)
SYS-JTMS-SWDIO: SWDIO.TP, U1.72 (PA13)
SYS-JTRST: JTRST.TP, U1.90 (PB4)
TX: R31.2, TX.TP
UART-RX: R32.2, U1.64 (PC7)
UART-RX-ENABLE: U1.60 (PD13), U6.1 (OE)
UART-TX: R29.1, U1.63 (PC6)
UART-TX-ENABLE: U1.58 (PD11), U5.1 (OE)
USB-D+: R19.2, U1.71 (PA12)
USB-D-: R20.2, U1.70 (PA11)
USB-ID: D2.1, U1.69 (PA10)
USB-VBUS: R21.2, R22.1, U1.68 (PA9)
USB-VBUS-5V: D2.6, R21.1
VCAP_1: C51.1, U1.48 (VCAP_1)
VCAP_2: C54.1, U1.73 (VCAP_2)
VCC: C7.1, C8.1, C9.1, C10.+, C11.+, C13.1, C18.1, C20.1, C24.1, D3.1 (A2), JP1.1, PS1.2 (VCC_1), PS1.3 (VCC_2), PS1.11 (VCC_3), R15.2, U3.1 (VS), U3.23 (VS), U3.43 (VS), U3.55 (VS), U3.66 (VS)
VCC-POWERSTEP: C15.1, JP3.1, U3.58 (VCC)
VCCREG: C25.1, JP3.2, U3.60 (VCCREG)
VDD: C17.1, JP2.2, R26.2, R28.2, U3.13 (VDDIO)
VDDA: C46.1, C48.1, R12.2, U1.22 (VDDA)
VREG: C16.1, C22.1, JP2.1, U3.62 (VREG)
VSREG: C14.1, JP1.2, U3.61 (VSREG)
VSW: C26.1, D1.1 (K), L1.1, PS1.1 (VSW_1), PS1.12 (VSW_2), PS1.13 (VSW_3), PS1.16 (VSW_4)

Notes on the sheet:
For VBAT
Tantalum
For each VDD
For VS
For each VS pad
For VCC pin on POWERSTEP01
For VDD
For VDDIO
For Stepper Driver IC
Power LED
POWERStep LED
For Stepper

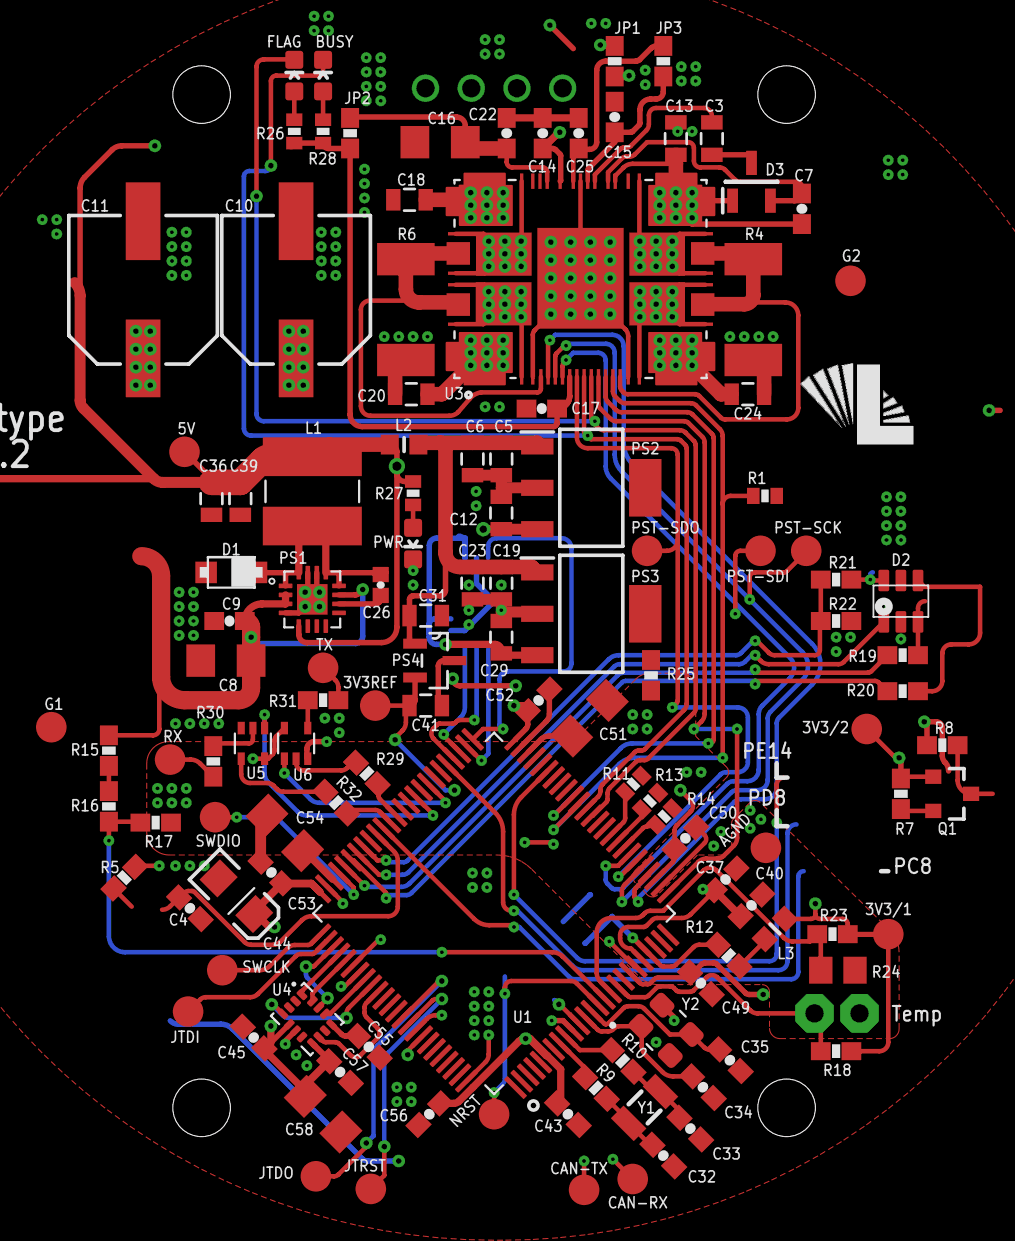
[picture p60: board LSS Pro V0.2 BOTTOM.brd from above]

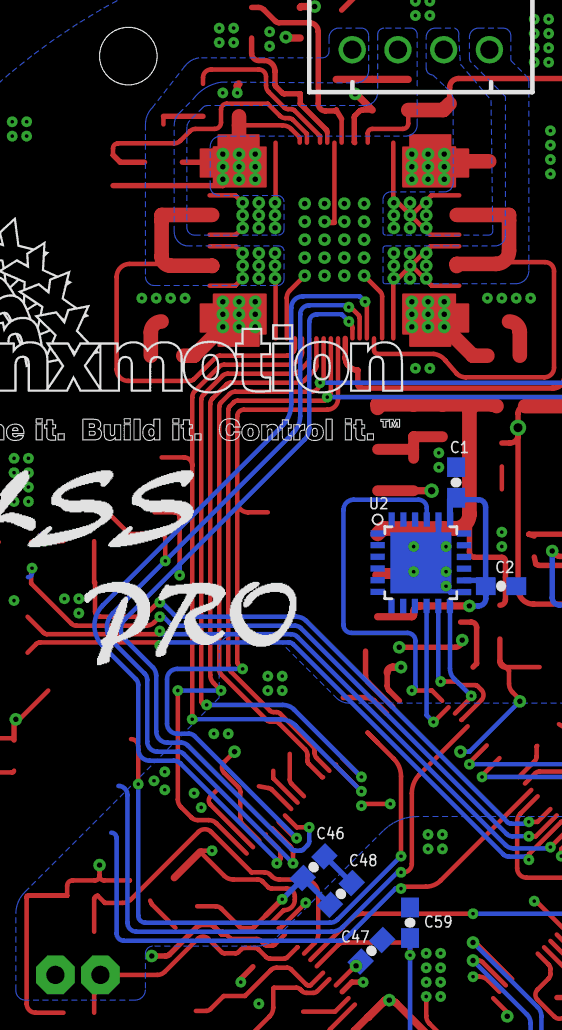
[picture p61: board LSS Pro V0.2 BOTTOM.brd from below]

Board: 4 copper layers, 131 parts (8 on the bottom side), 92 nets.

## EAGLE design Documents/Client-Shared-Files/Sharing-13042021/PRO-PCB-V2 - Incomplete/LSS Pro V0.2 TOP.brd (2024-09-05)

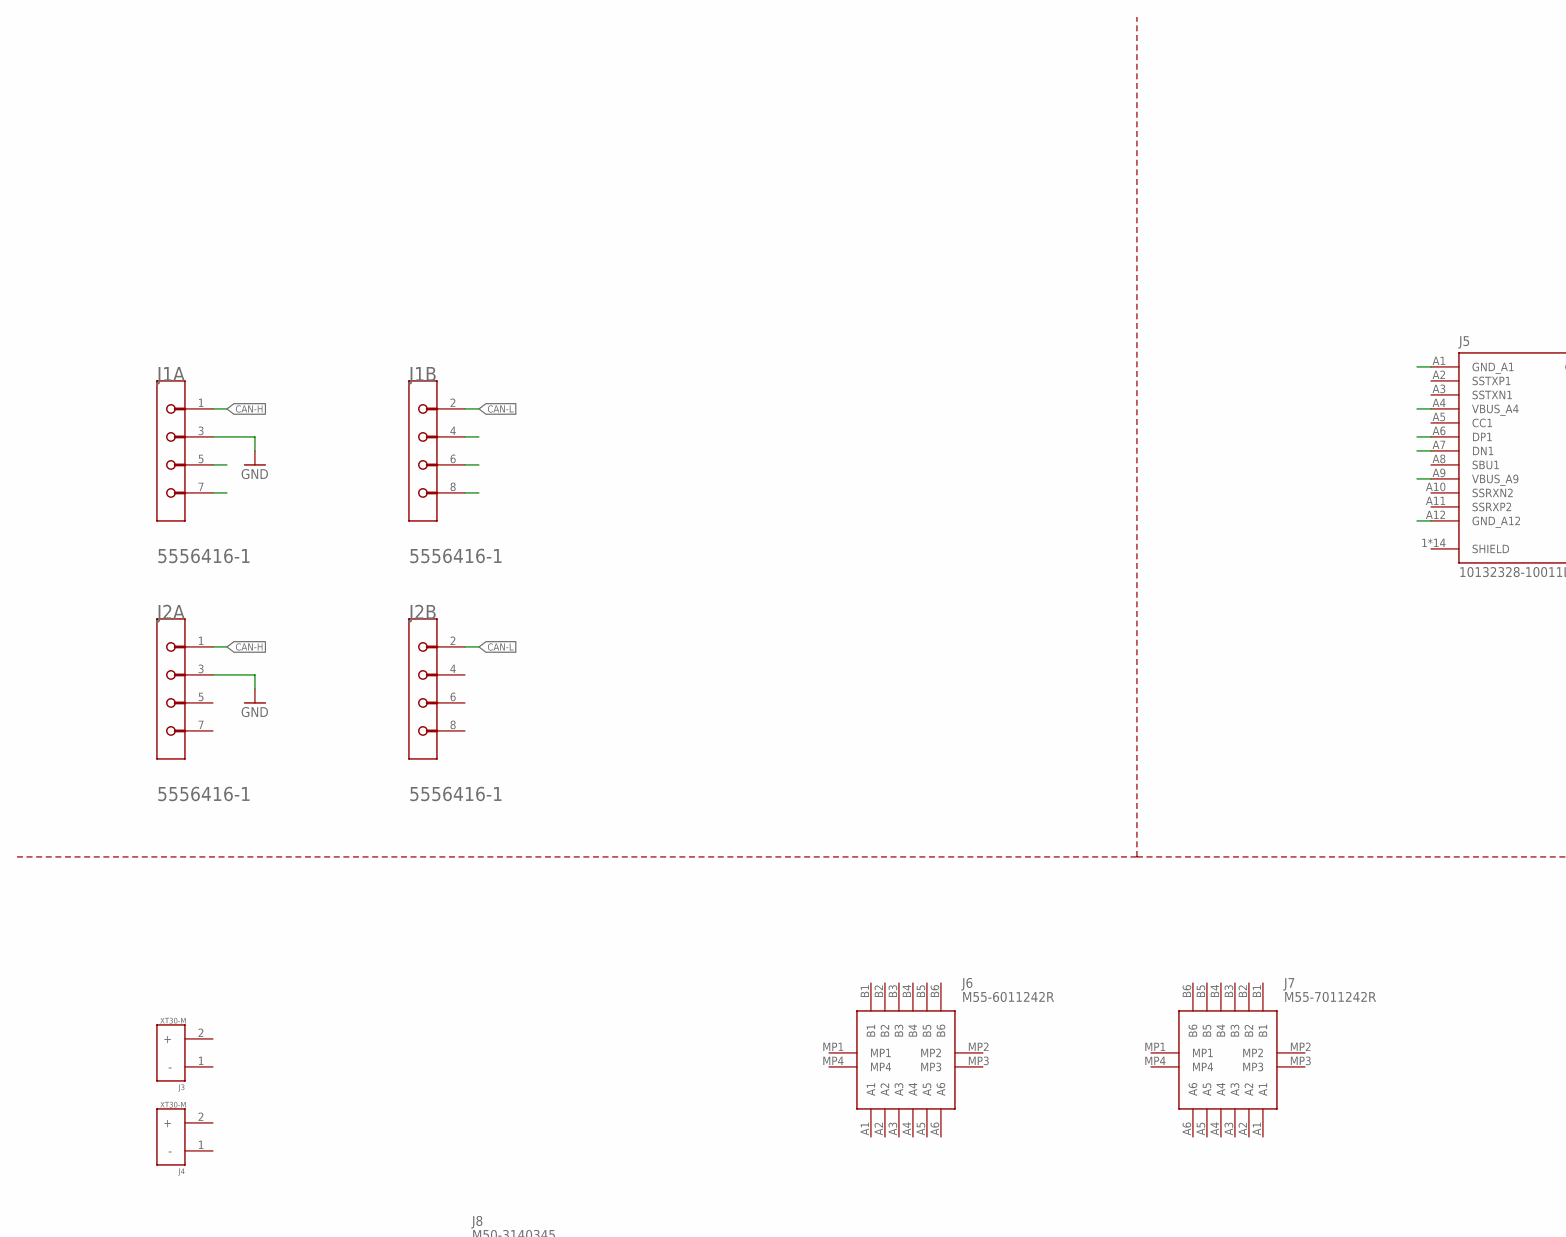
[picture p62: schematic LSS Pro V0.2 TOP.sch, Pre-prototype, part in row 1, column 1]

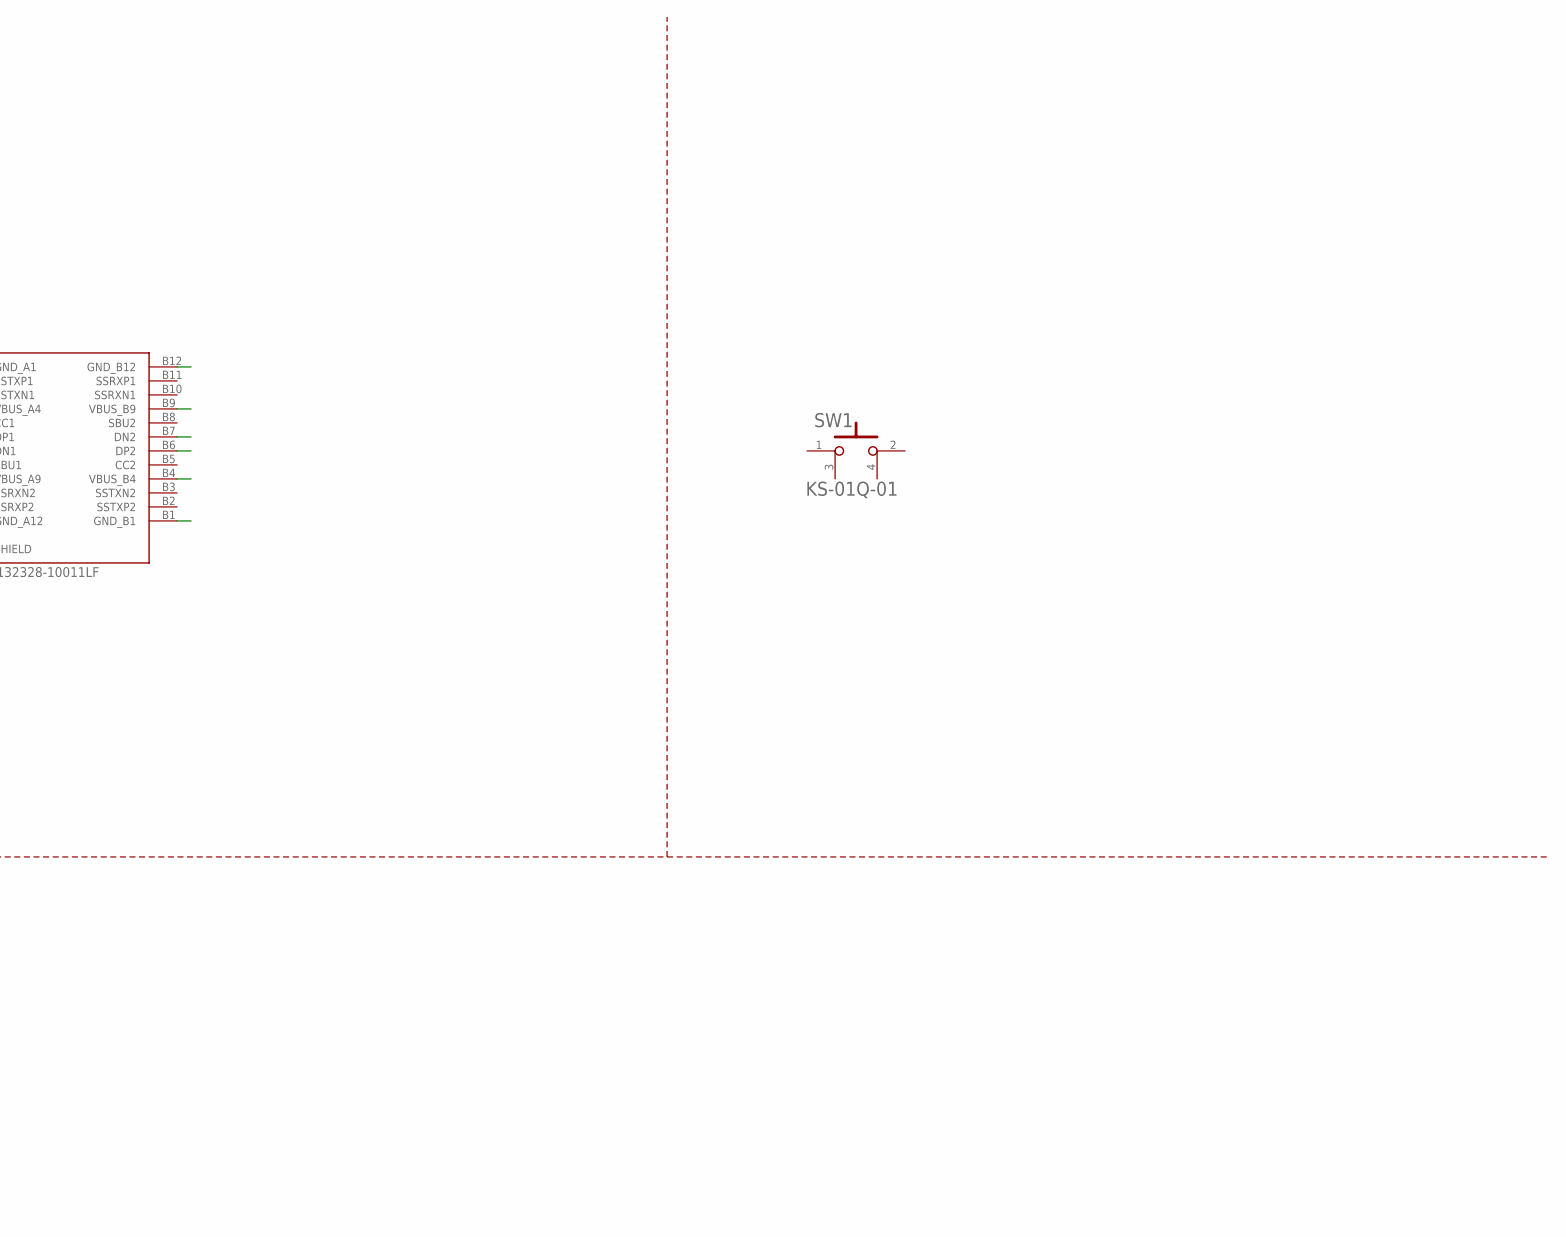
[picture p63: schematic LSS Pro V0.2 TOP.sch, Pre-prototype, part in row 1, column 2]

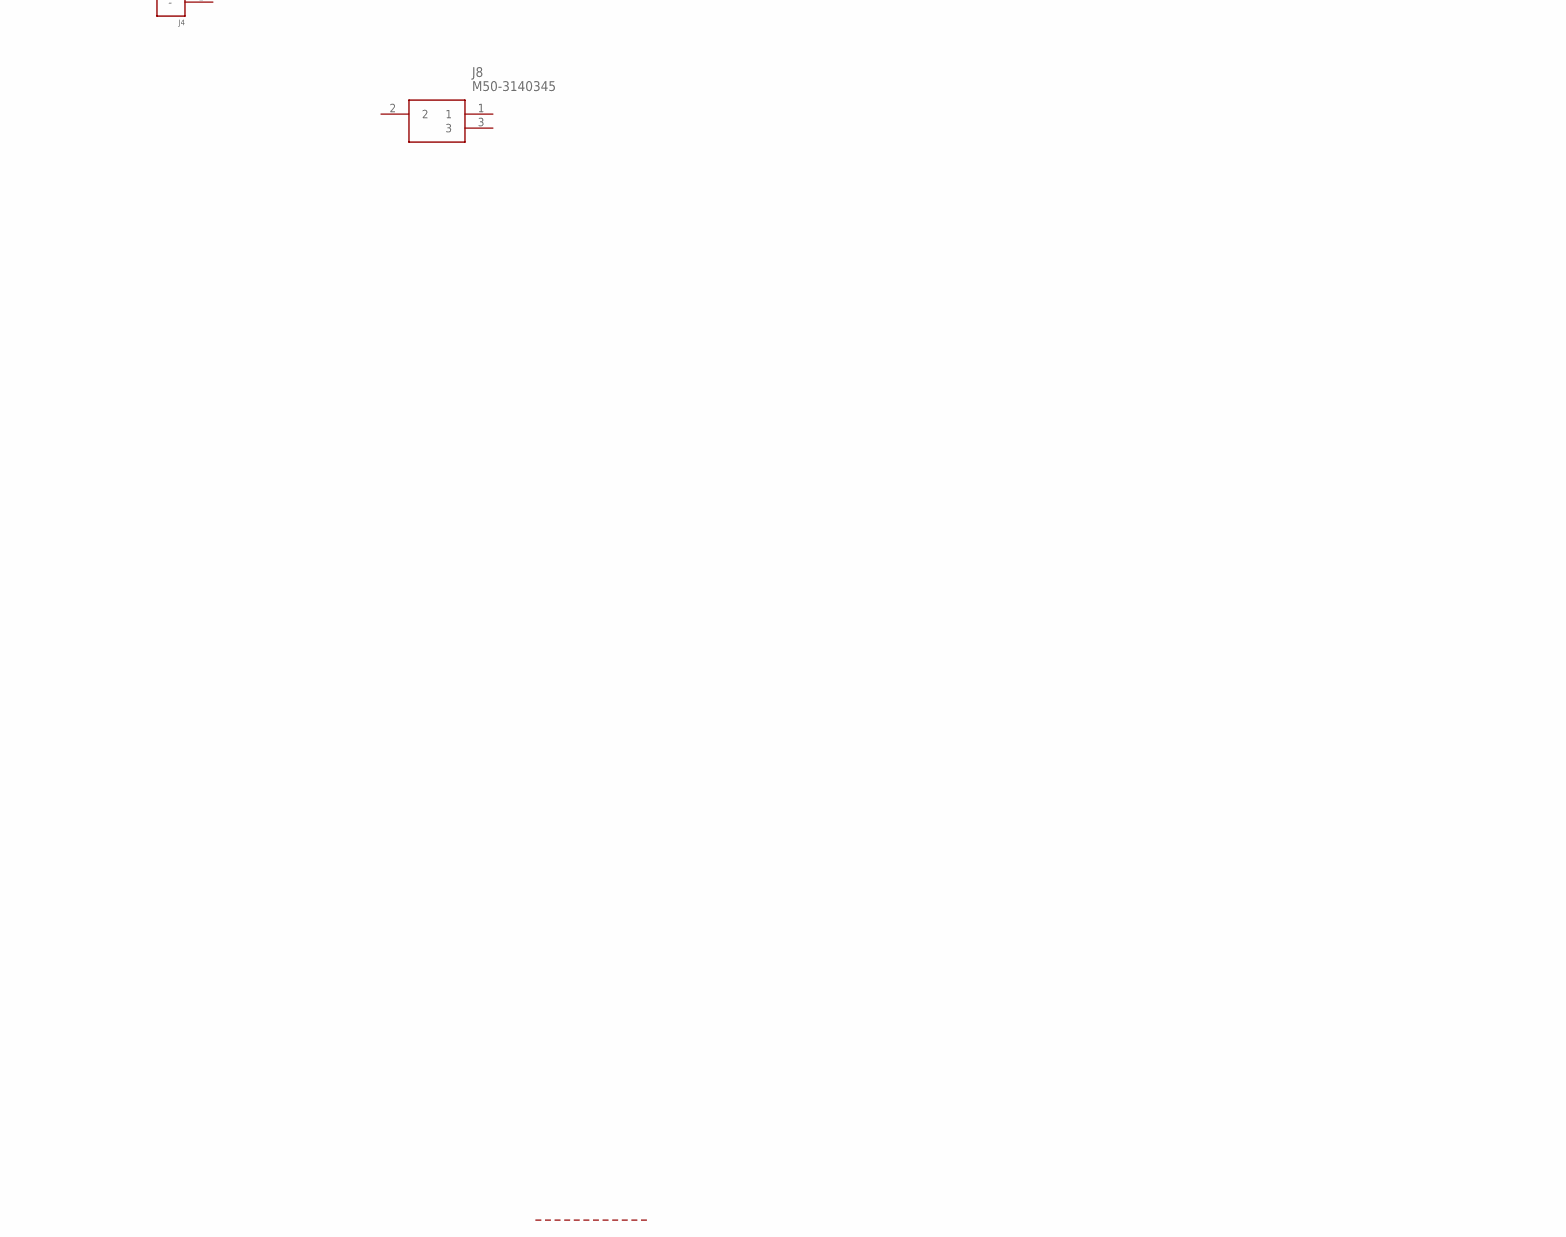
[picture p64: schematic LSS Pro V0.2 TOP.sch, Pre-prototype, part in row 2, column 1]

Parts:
J1, J2: TE_5556416-1TE_5556416-1_0_0; TE_5556416-1_0
J3, J4: XT30-M
J5: 10132328-10011LF; AMPHENOL_10132328-10011LF
J6: M55-6011242R; M556011242R
J7: M55-7011242R; M557011242R
J8: M50-3140345; M503140345
SW1: E-SWITCH_KS-01Q-01E-SWITCH_KS-01Q-01_0_0; E-SWITCH_KS-01Q-01_0

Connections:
CAN-H: J1.1, J2.1
CAN-L: J1.2, J2.2
GND: J1.3, J2.3

Board: 4 copper layers, 9 parts (0 on the bottom side), 3 nets, no tracks yet.

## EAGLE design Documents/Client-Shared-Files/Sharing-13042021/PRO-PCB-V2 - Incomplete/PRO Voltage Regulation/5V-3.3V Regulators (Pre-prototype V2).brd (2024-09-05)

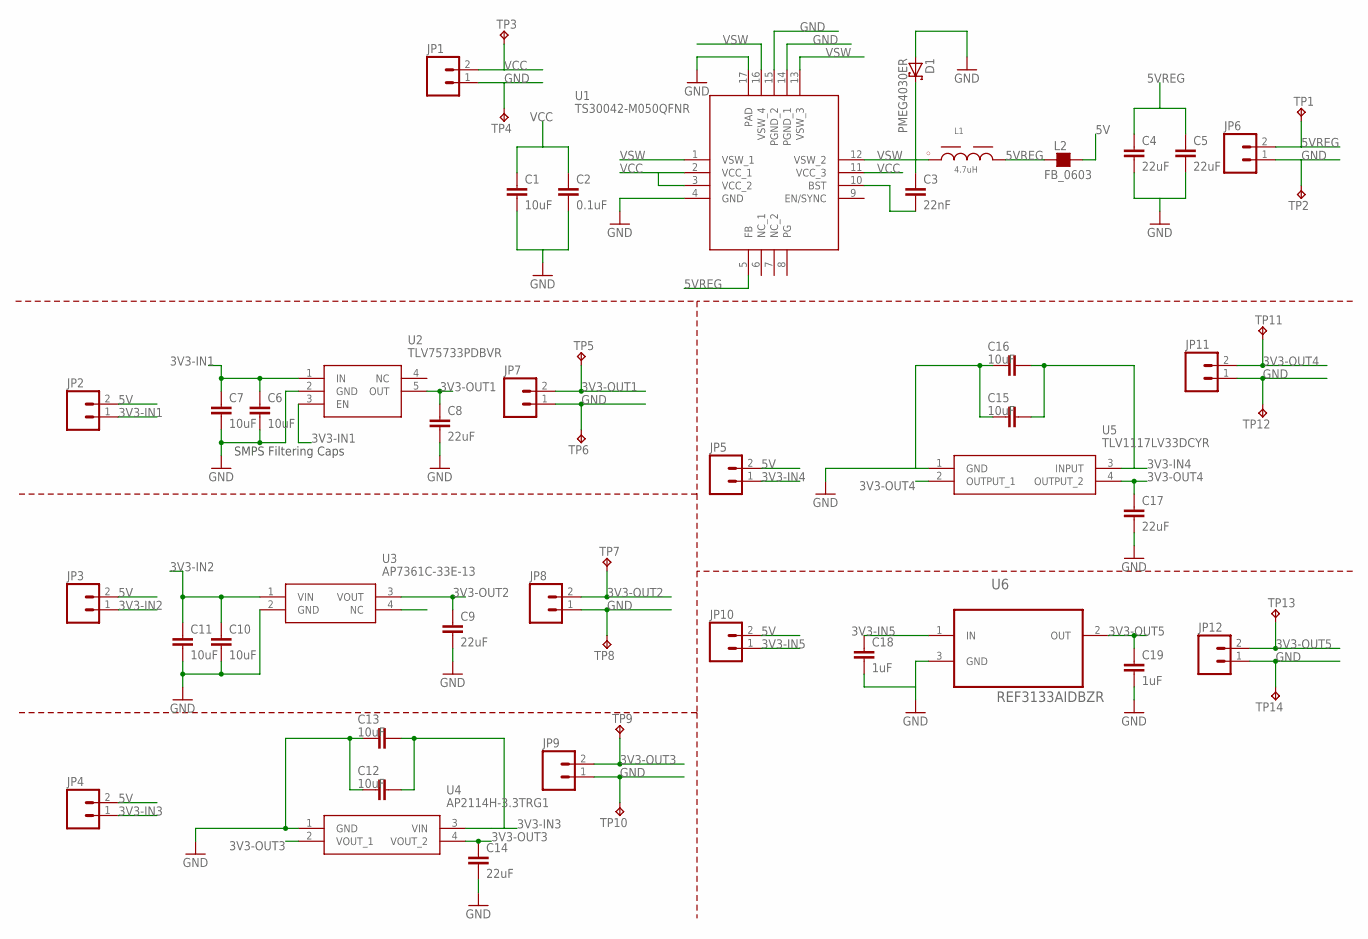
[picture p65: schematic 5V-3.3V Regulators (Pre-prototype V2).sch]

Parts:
C1: 10uF; 1206
C2: 0.1uF; 0603-CAP
C3: 22nF; 0402-CAP
C4, C5, C8, C9, C14, C17: 22uF; 0805
C6, C7, C10, C11, C12, C13, C15, C16: 10uF; 0805
C18, C19: 1uF; 0805
D1: PMEG4030ER; SOD123W
JP1, JP2, JP3, JP4, JP5, JP6, JP7, JP8, JP9, JP10, JP11, JP12: M02PTH; 1X02
L1: 4.7uH; WE-PD2_5848/5820
L2: FB_0603; L0603
TP1, TP2, TP3, TP4, TP5, TP6, TP7, TP8, TP9, TP10, TP11, TP12, TP13, TP14: TP-040
U1: TS30042-M050QFNR; QFN16
U2: TLV75733PDBVR; SOT95P280X145-5N
U3: AP7361C-33E-13; SOT230P700X165-4N
U4: AP2114H-3.3TRG1; SOT230P700X180-4N
U5: TLV1117LV33DCYR; SOT230P700X180-4N
U6: REF3133AIDBZR; SOT95P237X112-3N

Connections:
3V3-IN1: C6.1, C7.1, JP2.1, U2.1 (IN), U2.3 (EN)
3V3-IN2: C10.1, C11.1, JP3.1, U3.1 (VIN)
3V3-IN3: C12.1, C13.1, JP4.1, U4.3 (VIN)
3V3-IN4: C15.1, C16.1, JP5.1, U5.3 (INPUT)
3V3-IN5: C18.1, JP10.1, U6.1 (IN)
3V3-OUT1: C8.1, JP7.2, TP5.1, U2.5 (OUT)
3V3-OUT2: C9.1, JP8.2, TP7.1, U3.3 (VOUT)
3V3-OUT3: C14.1, JP9.2, TP9.1, U4.2 (VOUT_1), U4.4 (VOUT_2)
3V3-OUT4: C17.1, JP11.2, TP11.1, U5.2 (OUTPUT_1), U5.4 (OUTPUT_2)
3V3-OUT5: C19.1, JP12.2, TP13.1, U6.2 (OUT)
5V: JP2.2, JP3.2, JP4.2, JP5.2, JP10.2, L2.2
5VREG: C4.1, C5.1, JP6.2, L1.2, L2.1, TP1.1, U1.5 (FB)
GND: C1.2, C2.2, C4.2, C5.2, C6.2, C7.2, C8.2, C9.2, C10.2, C11.2, C12.2, C13.2, C14.2, C15.2, C16.2, C17.2, C18.2, C19.2, D1.2 (A), JP1.1, JP6.1, JP7.1, JP8.1, JP9.1, JP11.1, JP12.1, TP2.1, TP4.1, TP6.1, TP8.1, TP10.1, TP12.1, TP14.1, U1.4 (GND), U1.14 (PGND_1), U1.15 (PGND_2), U1.17 (PAD), U2.2 (GND), U3.2 (GND), U4.1 (GND), U5.1 (GND), U6.3 (GND)
unnamed: C3.2, U1.10 (BST)
VCC: C1.1, C2.1, JP1.2, TP3.1, U1.2 (VCC_1), U1.3 (VCC_2), U1.11 (VCC_3)
VSW: C3.1, D1.1 (K), L1.1, U1.1 (VSW_1), U1.12 (VSW_2), U1.13 (VSW_3), U1.16 (VSW_4)

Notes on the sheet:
SMPS Filtering Caps

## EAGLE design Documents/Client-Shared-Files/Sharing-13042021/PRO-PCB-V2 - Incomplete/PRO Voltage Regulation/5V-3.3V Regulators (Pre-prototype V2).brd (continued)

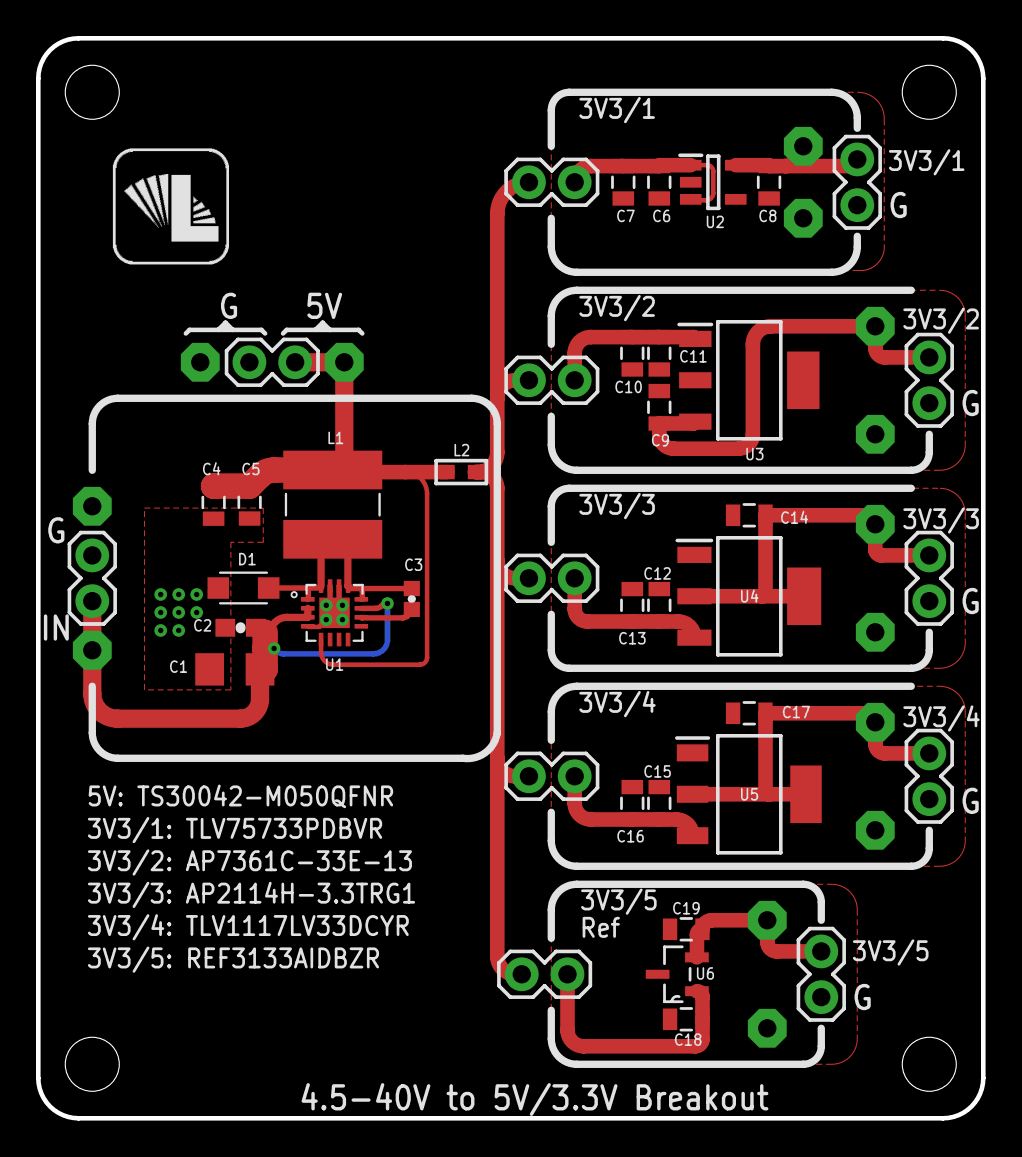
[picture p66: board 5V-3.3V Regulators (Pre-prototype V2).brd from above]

Board: 2 copper layers, 52.5 x 60.0 mm, 54 parts (0 on the bottom side), 16 nets.

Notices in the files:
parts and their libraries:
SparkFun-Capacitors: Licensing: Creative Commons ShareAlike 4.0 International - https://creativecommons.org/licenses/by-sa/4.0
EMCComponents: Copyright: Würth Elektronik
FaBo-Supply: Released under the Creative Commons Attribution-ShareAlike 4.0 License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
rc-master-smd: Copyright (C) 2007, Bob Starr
